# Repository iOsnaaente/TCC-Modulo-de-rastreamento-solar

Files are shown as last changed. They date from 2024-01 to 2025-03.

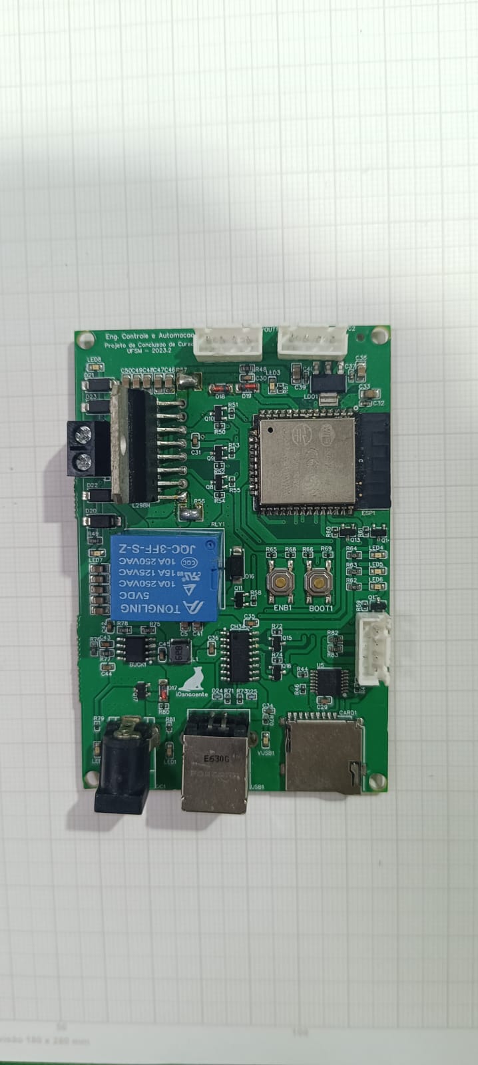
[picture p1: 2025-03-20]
Imagens/PCB_visão superior.jpg

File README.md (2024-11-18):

# TCC
Projeto de hardware para desenvolvimento de um módulo de controle de motor DC com sensor de posição angular para movimentação de paineis solares em dois eixos utilizando rede Modbus.

### Description 

The [bdc_motor](https://components.espressif.com/component/espressif/bdc_motor), 
The [PID component](https://components.espressif.com/component/espressif/pid_ctrl) is also managed by the component manager. 
These components' dependencies are listed in the [manifest file](main/idf_component.yml).

### Hardware Required

* A iOsnaaente TCC board with the ESP32-WROOM32E;
* A USB cable for Power supply and programming type micro-B;
* A separate 12 or 24V power supply for brushed DC motor;   
* H-bridge L298N datasheet used on board;
* A brushed DC motor connected in output borne on TCC board;
* A quadrature encoder of type AB to detect speed and direction of turns.

### Connection MCPWM + Encoder :
```
                              Battery power (8.4V - 24V)       
                                         |
      ESP 32                             v   L298N                   _
+-------------------+             +--------------------+            | |
|                   |             |      H-Bridge      |            | |
|               GND +<----------->| GND                |      +--------------+
|                   |             |      Chanel 1      |      |              |
|            GPIO_A +----GPIO0--->+ IN_A         OUT_A +----->|   Brushed    |
|            GPIO_B +----GPIO1--->+ IN_B               |      |     DC       |
|           BDC_PWM +----PWM0B--->+ PWM          OUT_B +----->|    Motor     |
|                   |             |                    |      |              |
|                   |             +--------------------+      |              |
|                   |                                         +------+-------+
|                   |                Encoder based                   |
|                   |                   on PCNT                      |
|                   |             +--------------------+             |
|            VCC3.3 +------------>+ VCC    Encoder     |             |
|                   |             |                    |             |
|               GND +<----------->+ GND                +<------------+
|                   |             |                    |
|         ENCODER_A |<---PCNT1----+ C1                 |
|         ENCODER_B |<---PCNT1----+ C2                 |
|                   |             |                    |
|                   |             |                    |
|                   |             |                    |
+-------------------+             +--------------------+
```

### MODBUS NETWORK 

Modbus multi slave segment connection schematic:

```
    MB_DEVICE_ADDR1
    -------------
    |           |
    |  Slave 1  |---<>--+
    |           |       |
    -------------       |
    MB_DEVICE_ADDR2     |
    -------------       |        -------------
    |           |       |        |           |
    |  Slave  2 |---<>--+---<>---|  Master   |
    |           |       |        |           |
    -------------       |        -------------
    MB_DEVICE_ADDR3     |
    -------------     Network (Ethernet or WiFi connection)
    |           |       |
    |  Slave 3  |---<>--+
    |           |
    -------------
```

### Steps 

[1] Fazer a definição dos pinouts de motores e encoders
    - IN1, IN2 e PWM para motores
    - ENC_A e ENC_B para o encoder de quadratura 

[2] Inicializar os pinouts apropriadamente 
    - Pinos de motores como OUTPUT
    - Pinos de sensor como INPUT 

[3] Inicializar as configurações do motor
    - Instaciar a struct motor_t 

[4] Inicializar as configurações do encoder
    - Instanciar a struct encoder_t 

[5] Criar a rotina de calculo da velocidade
    - Task ou Timer interrupt 

### Tutorials 

To learn more about Motor Controle PWM (MCPWM) see: 
[1] https://docs.espressif.com/projects/esp-idf/en/v4.4/esp32/api-reference/peripherals/mcpwm.html
[2] https://demo-dijiudu.readthedocs.io/en/latest/api-reference/peripherals/mcpwm.html

To learn more about Pulse CoNTer (PCNT) see: 
[1] https://demo-dijiudu.readthedocs.io/en/latest/api-reference/peripherals/mcpwm.html

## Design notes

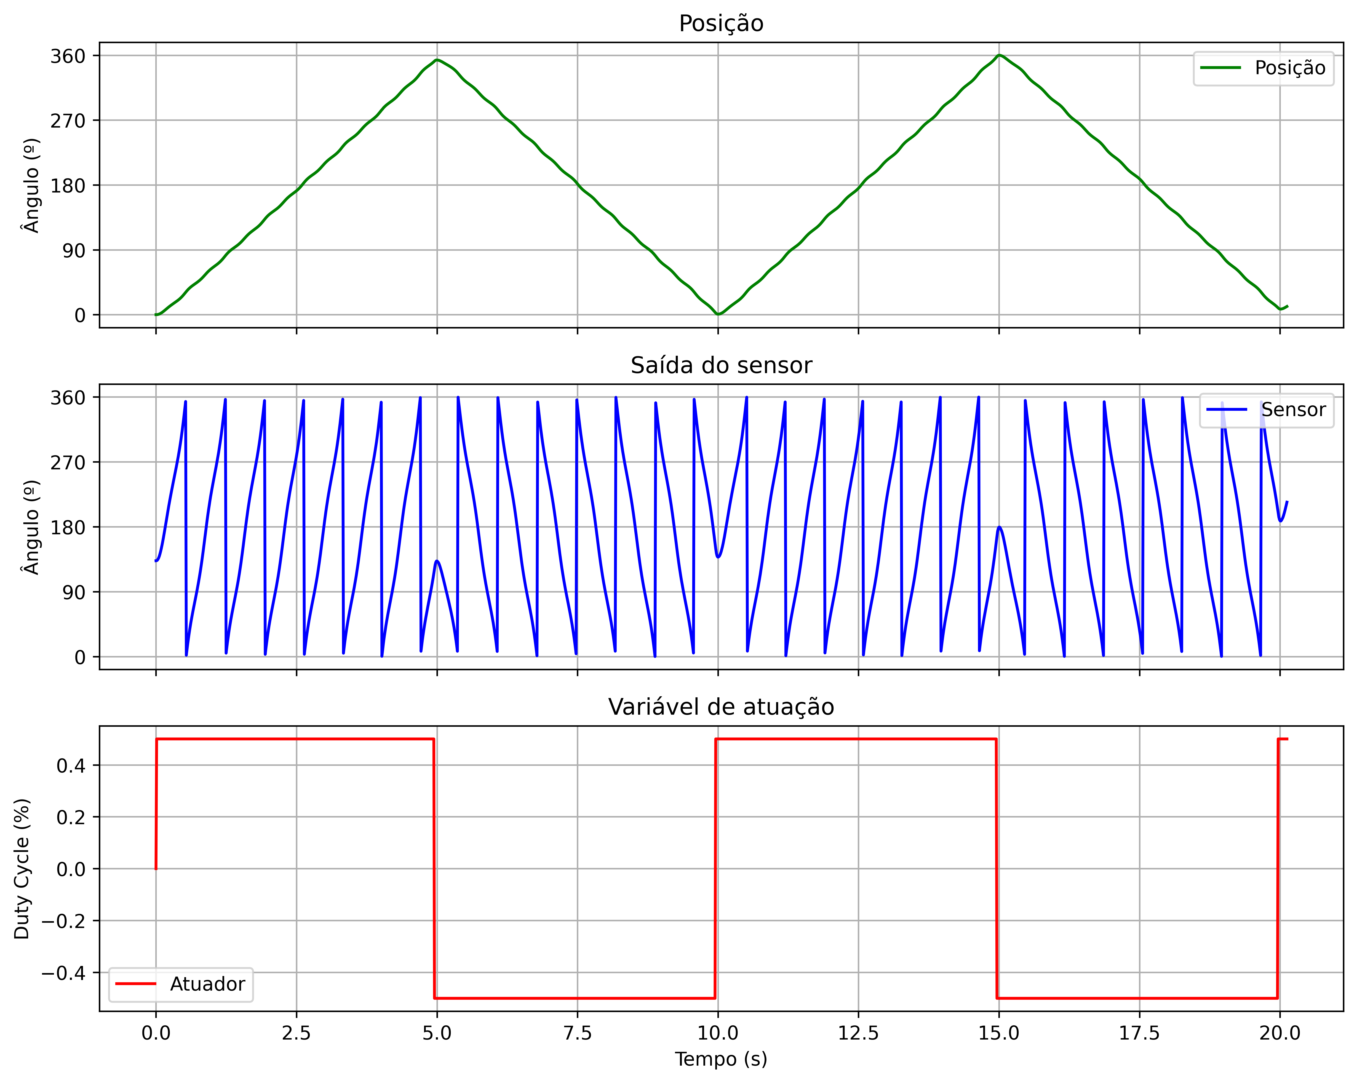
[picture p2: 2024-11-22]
Imagens/SensorMagnetico.png

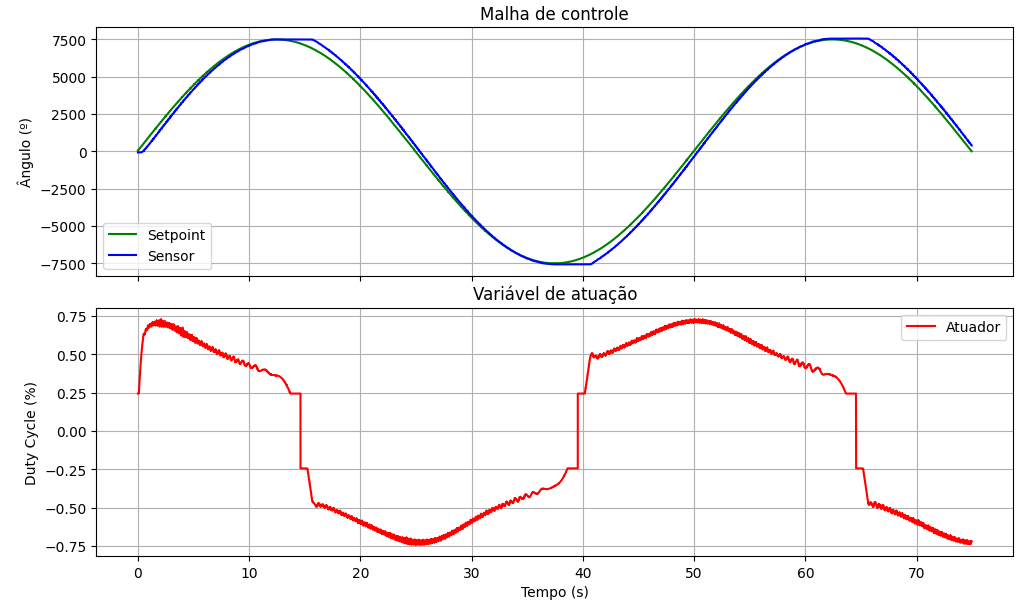
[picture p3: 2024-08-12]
Imagens/ControleSenoide.png

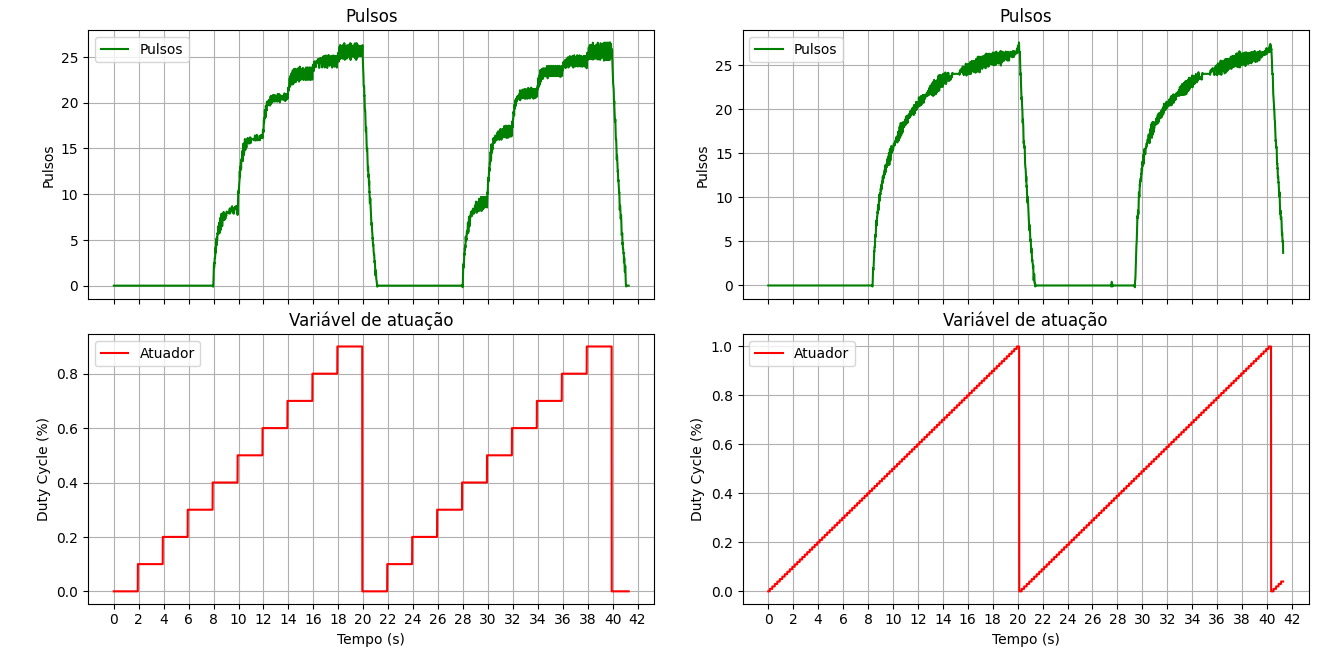
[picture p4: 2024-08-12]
Imagens/SensorIncremental.png

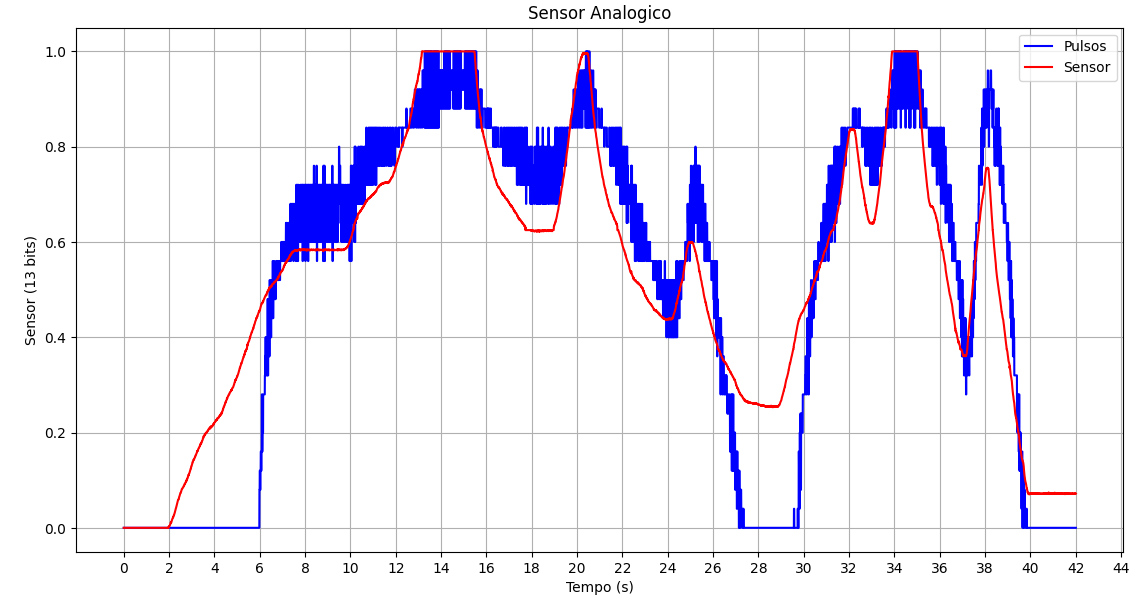
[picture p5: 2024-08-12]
Imagens/SensorAnalogico.png

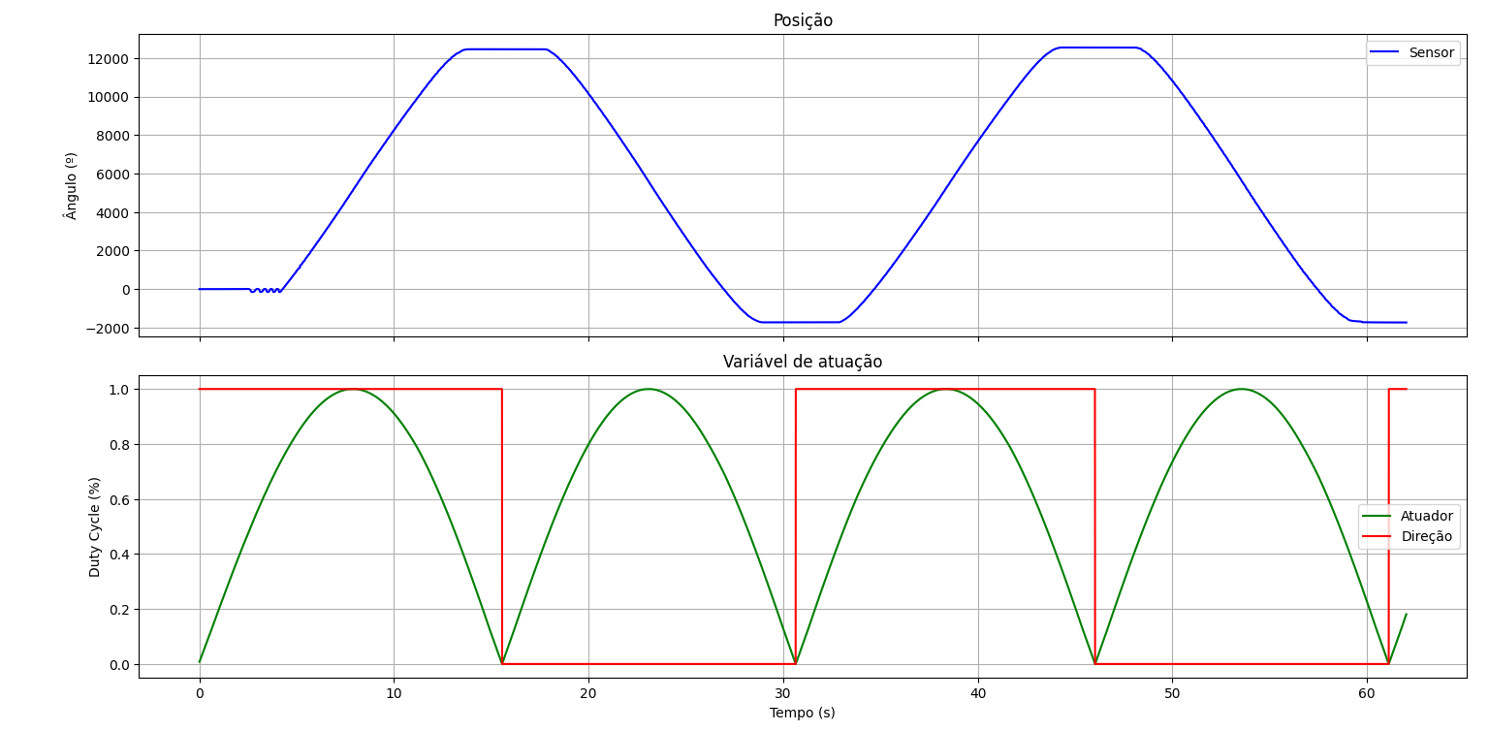
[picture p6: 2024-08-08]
Imagens/AtuadorDC.png

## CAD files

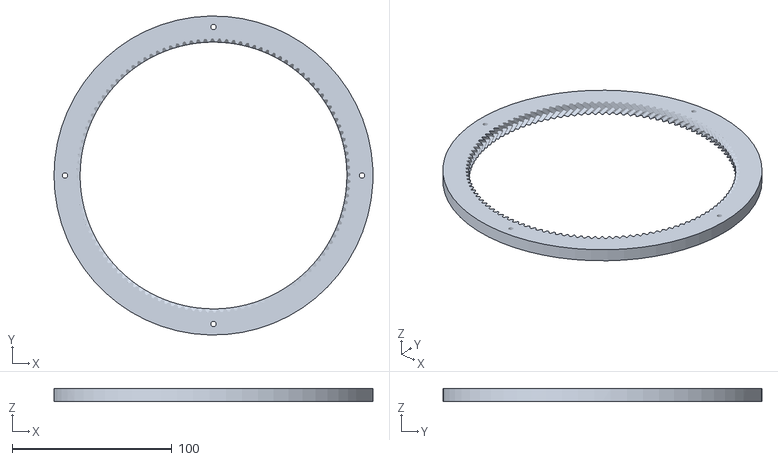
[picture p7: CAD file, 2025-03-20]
Modelos3D/3_Reducao_Anel.STL
200.0 x 199.9 x 8.00

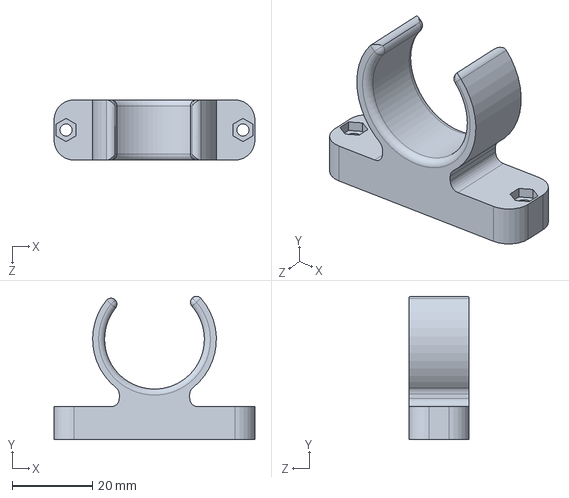
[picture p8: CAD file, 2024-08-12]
Modelos3D/3D/SUP_INC.SLDPRT
50.0 x 35.7 x 15.0 mm

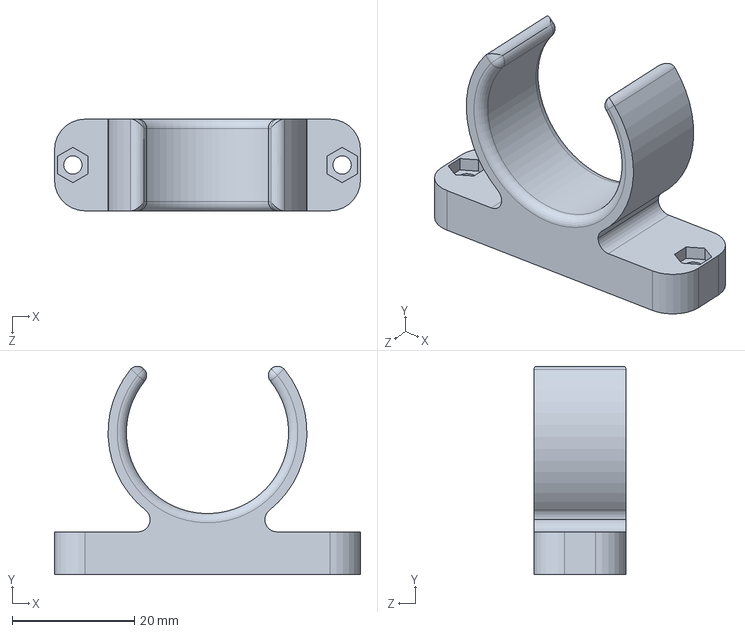
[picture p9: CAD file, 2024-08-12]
Modelos3D/3D/SUP_MAG.SLDPRT
50.0 x 34.1 x 15.0 mm

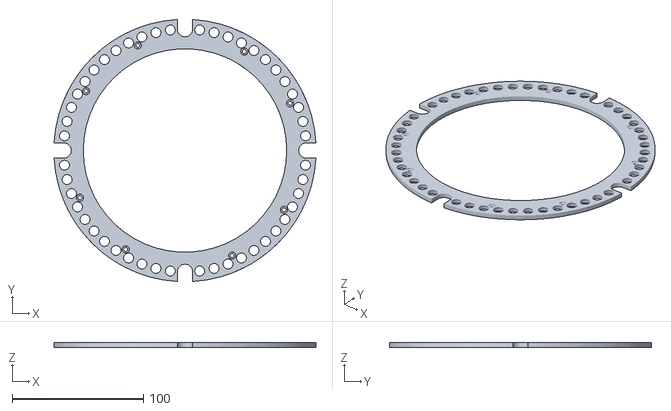
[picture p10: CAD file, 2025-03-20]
Modelos3D/Cópia de Peça2^Mont4.STL
199.7 x 199.7 x 3.50

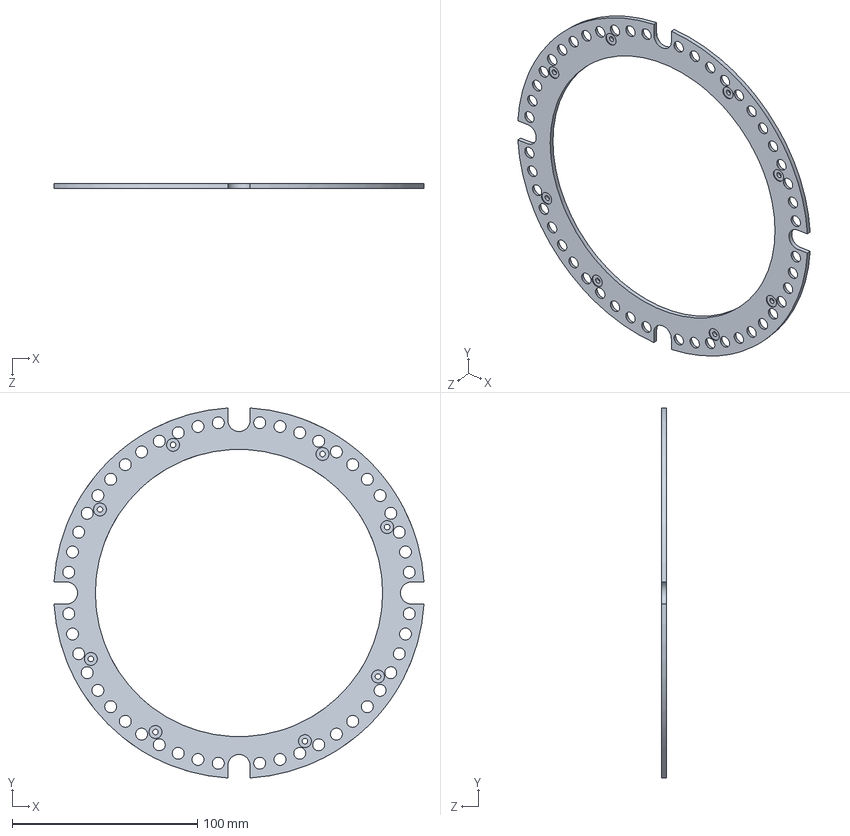
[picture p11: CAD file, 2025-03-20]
Modelos3D/Peça2^rolamentoCase2.SLDPRT
199.6 x 199.6 x 2.50 mm

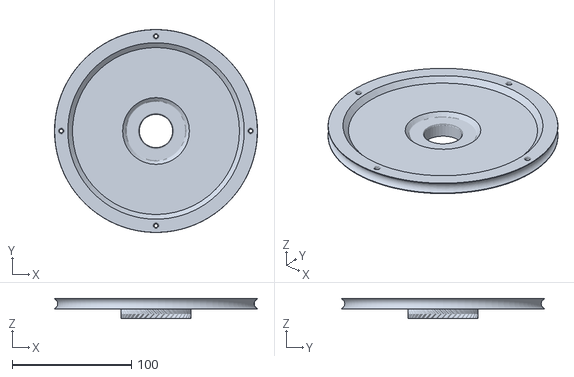
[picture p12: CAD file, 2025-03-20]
Modelos3D/anel_interno_Engrenagens.STL
170.2 x 170.1 x 17.0

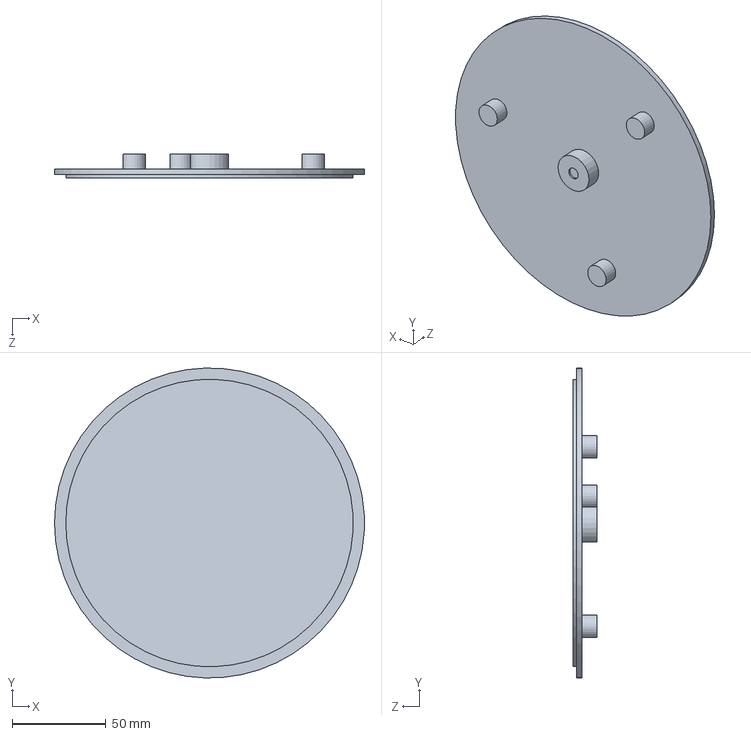
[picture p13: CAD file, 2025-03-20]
Modelos3D/P_Superior.SLDPRT
165.0 x 164.9 x 13.0 mm

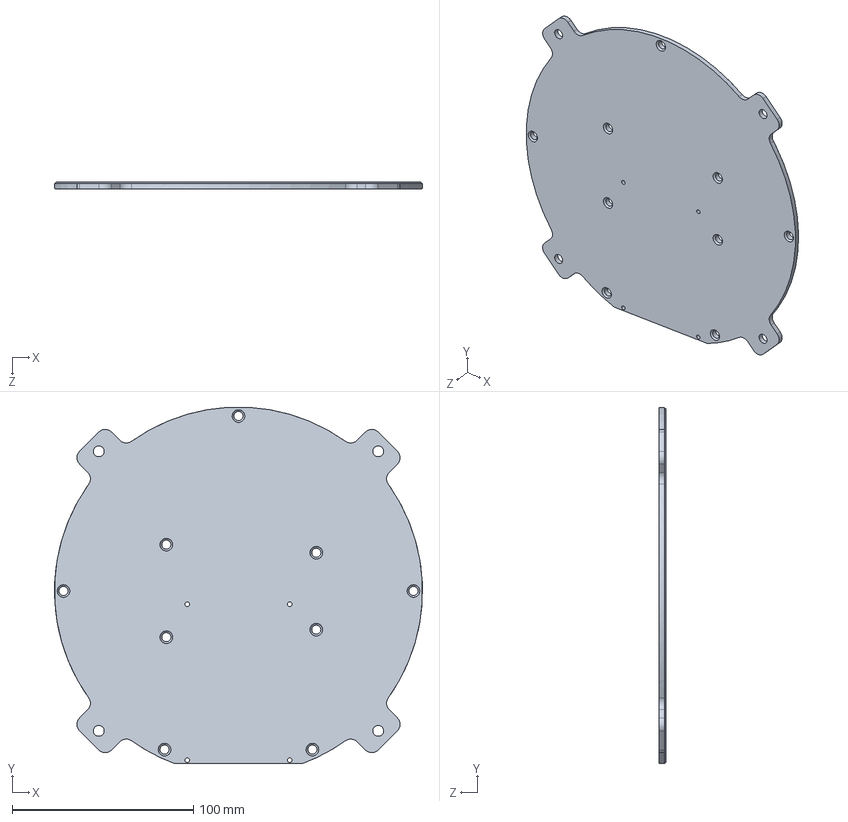
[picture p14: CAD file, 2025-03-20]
Modelos3D/Base_Estrutura.SLDPRT
203.0 x 196.6 x 4.00 mm

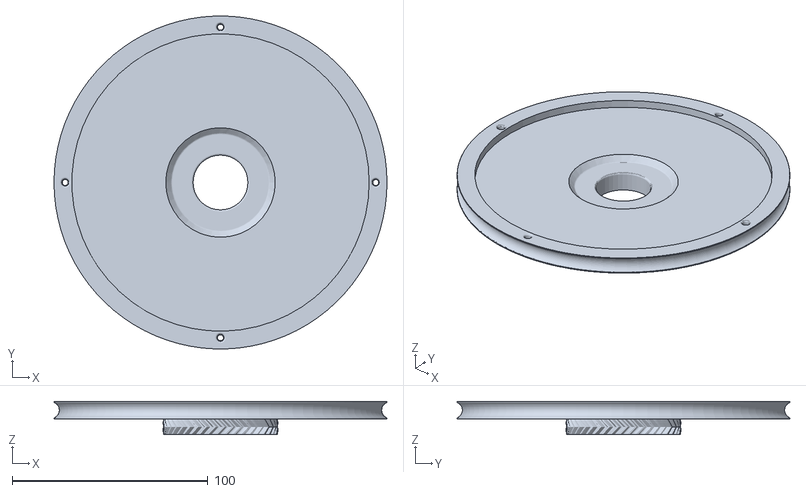
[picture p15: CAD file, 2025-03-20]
Modelos3D/1_Anel_Interno_Engrenagens.STL
170.2 x 170.1 x 17.0

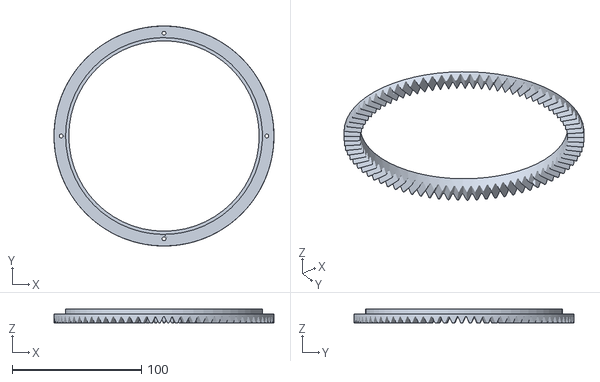
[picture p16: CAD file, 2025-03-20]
Modelos3D/2_Anel_Interno_Rosca.STL
169.9 x 169.9 x 11.0

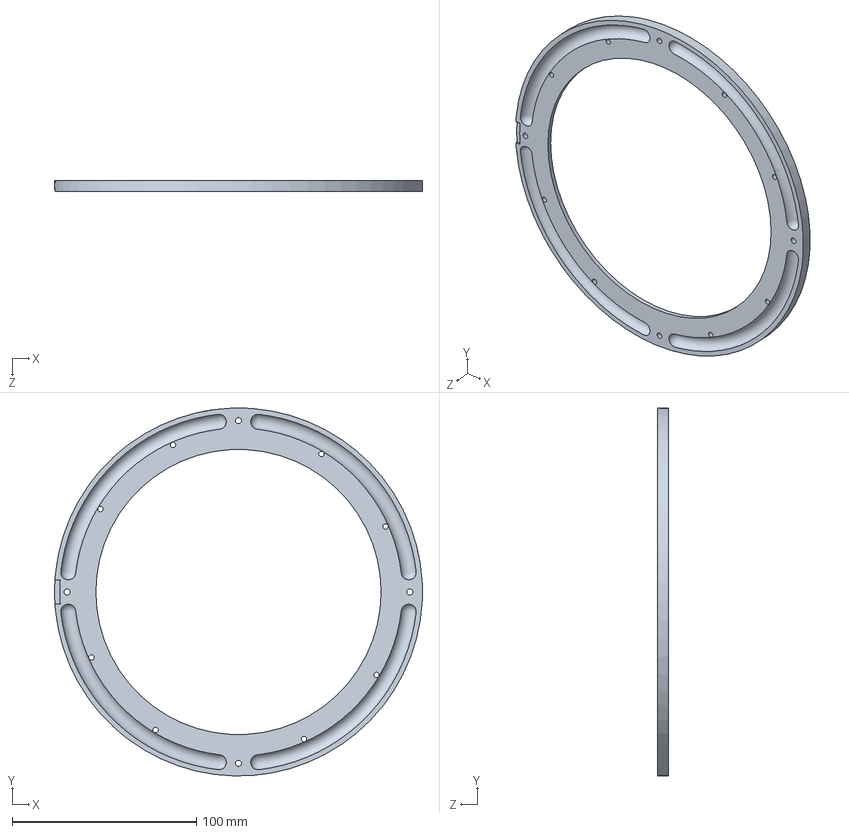
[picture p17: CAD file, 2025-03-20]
Modelos3D/P_Tampa1.SLDPRT
200.0 x 199.9 x 6.00 mm

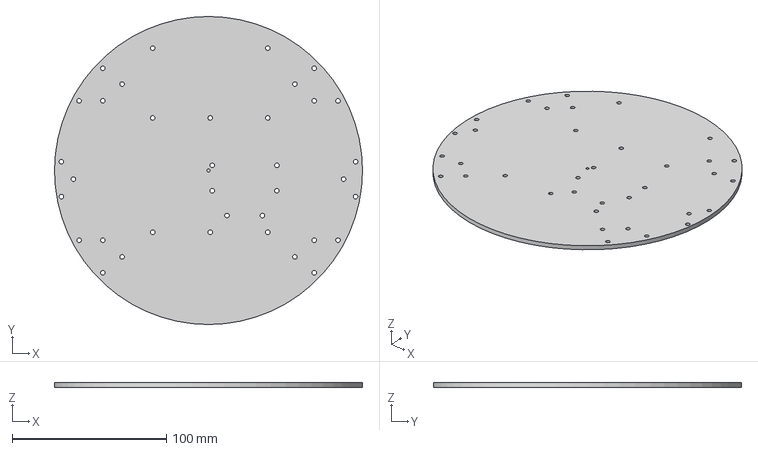
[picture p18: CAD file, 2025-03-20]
Modelos3D/furos.step
200.0 x 200.0 x 3.00 mm

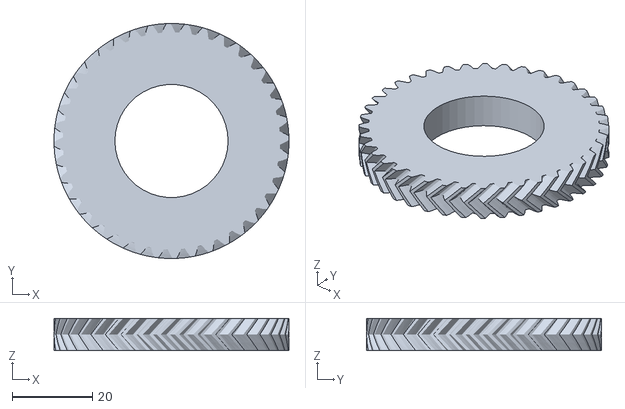
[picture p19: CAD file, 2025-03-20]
Modelos3D/Engrenagem_planeta.STL
58.6 x 58.6 x 8.00

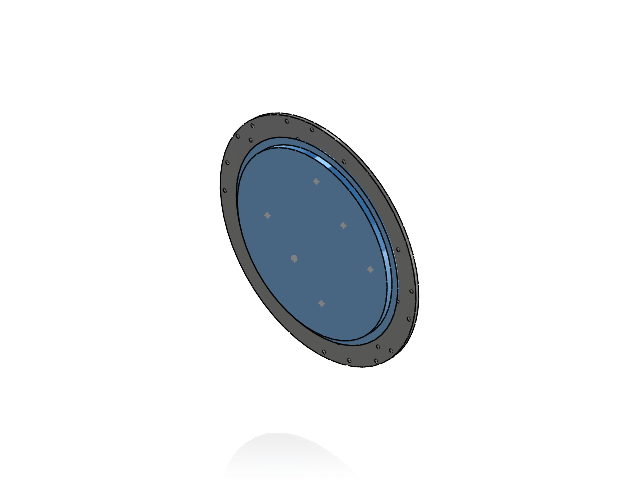
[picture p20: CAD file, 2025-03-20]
Modelos3D/Mont5.SLDASM
Superior
Componente27.step

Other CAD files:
Modelos3D/Reducao_Sol.SLDASM
Modelos3D/Mont4.SLDASM
Modelos3D/rolamentoCase.SLDASM
Modelos3D/Peça2^rolamentoCase.STL
Modelos3D/3D/SUP_INC.STL
Modelos3D/3D/SUP_MAG.STL
Modelos3D/Base_Estrutura.STL
Modelos3D/P_Tampa.SLDPRT
Modelos3D/P_Tampa.STL
Modelos3D/Superior.SLDPRT
Modelos3D/Superior.STL
Modelos3D/Tampa.SLDPRT
Modelos3D/Tampa.STL
Modelos3D/anel_interno_2.STL
Modelos3D/furos.SLDASM

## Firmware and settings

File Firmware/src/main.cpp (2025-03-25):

/**
  * @file main.cpp
  * @brief Entry Point do Firmware de controle 
  * @author Bruno Gabriel Flores Sampaio
  * @date 16 de março de 2025
  */

/** Board configurations */
#include "../board_config.h"

/** Controladores */
#include "controllers/includes/dataloggerController.h"
#include "controllers/includes/modbusController.h"
#include "controllers/includes/motorController.h"
#include "controllers/includes/serialController.h"

/** Módulos */
#include "modules/system/relay.h"


/** Objetos usados no sistema */
DataloggerController    *datalogger;
MotorController         *controller;
ModbusController        *modbus; 
Relay                   *relay;


// Contador para ser usado para debug
uint32_t debugger_counter = 0;

// Periodo para ser printado alguma informação via Terminal 
uint32_t debugger_period = 1000;

// Periodo do loop de verificação de estados 
uint32_t loop_period = 10;


void setup(){

    /** 
     * @brief Inicia a Serial para ser usada como Debug
     * @note Dentro de BoardConfig pode ser alterado o nível de Debug utilizado:
     * 1. DEBUG_SERIAL_COMPLETO 
     * 2. DEBUG_SERIAL_REDUZIDO 
     * 3. DEBUG_SERIAL_DESLIGADO 
    **/ 
    serial_begin( );

    /** 
     * @brief Inicia a comunicação WiFi para controle Modbus
     * 1. Inicia a interface Wi-Fi com Login e Senha definidos em BoardConfig
     * 2. Inicia a aplicação Modbus-TCP/IP utilizando a rede Wi-Fi
     * 3. Inicializa os registradores Modbus 
     * 4. Retorna o objeto Modbus para ser usado 
    **/ 
    DEBUG_SERIAL( "WIFI SSID", SSID_MASTER );
    modbus = new ModbusController( "ModbusController", RTC_SOFT );


    /** 
     * @brief Inicia o controle dos motores
     * @param description Descrição do objeto 
     * @param sensor_type Tipo de sensor para ser usado no módulo 
     * @param motor_type Tipo de motor utilizado no módulo 
     * 
     * 1. Inicializa a classe especifica do Sensor passado como parametro em SensorType_t 
     * 2. Inicializa a classe especifica do Motor passado como parametro em MotorType_t
     * 3. Cria a Task de controle de rastreamento do sistema
     * 
     * @note O tipo de rastreamento é dado pela MACRO definida em BoardConfig: 
     * - AZIMUTE_MODE - Modo de rastreio para Azimute 
     * - ZENITE_MODE - Modo de rastreio para Zenite 
    **/
    controller = new MotorController( "MotorController", SENSOR_AS5600_I2C, MOTOR_DC );  // controller->set_pid_gains( 10.25, 0.42, 4.78 );
    

    /**
     * @brief Define os valores de PID para a malha de controle do motor
     * @details A malha de controle é composta por um controlador em cascata, sendo composto por:
     * 1. Malha externa: Uma malha externa, que recebe o valor de referência do SP da planta (Posição);
     * 2. Malha interna: Uma malha interna que recebe a saída da primeira malha e faz o controle de velocidade do motor.
     * 
     * Dessa forma, a malha externa cuida da referência de posição, pois é a variavel de interesse do sistema e por consequencia,
     * é a malha mais lenta da planta, sua saída entra na malha de controle de velociade, uma malha rápida, que altera a
     * velocidade do motor para alcançar o objetivo do SP mais rápido.
     * 
     * Essa malha em cascata atingiu um bom resultado, sendo usado a medição de velocidade do motor ao invés do valor de 
     * corrente do mesmo, pois essa grandeza não pode ser medida de forma efetiva pelo módulo.   
     * 
     *                        double Kp, Ki, Kd
     **/ 
    controller->set_pos_pid_gains(  120.0, 100.0, 10.0 );
    // controller->set_vel_pid_gains(  1.0, 0.0, 0.0 );



    /** 
     * @brief Inicializa o Relé de proteção. 
    **/
    relay = new Relay( "Relay controller" );
    relay->turn_on();
    controller->stop();

    /** 
     * @brief Inicia a task do LED para debug visual
    **/
    xTaskCreate( &blink_Task, "BlinkTask", 1024*2, NULL, tskIDLE_PRIORITY, NULL );

}



/** 
 * @brief Loop principal 
 * 
 * Optou-se por utilizar o loop principal pois ele desempenha uma função simples, uma vez que as 
 * tarefas complexas de atuação, sensoriamento e controle do sistema, já estão sendo executadas
 * seguindo um Schedule do freeRTOS. 
 *  
 * A função do Loop esta relacionada com a comunicação Modbus do sistema, pois:
 * 1. Ele verifica de forma periodica se é necessário atualizar a Data e Hora do sistema;
 * 2. Ele verifica o estado de operação do sistema. 
 * 
 * @note Como o sistema será demonstrado como um caso de uso, criou-se estados de operação
 * que serão usados exclusivamente para a demonstração. Para uma aplicação real, pode-se criar 
 * estados mais complexos e que se adequem melhor à aplicação do mesmo.
 * 
 * Para a demonstração, será utilizado apenas um conjunto de estados que irão variar o SP da planta 
 * para valores fixos e conhecidos, permitindo mostrar a eficacia do sistema de controle e mostrando
 * que ele pode ser usado em um sistema de rastreamento solar. 
**/
void loop() {

    // Etapa 1: Verificar se é necessário atualizar a Data e Hora 
    if ( modbus->mb->Coil( COIL_DT_SYNC ) == true ){
        modbus->mb->Ireg( INPUT_YEAR,   modbus->mb->Hreg( HR_YEAR ) );
        modbus->mb->Ireg( INPUT_MONTH,  modbus->mb->Hreg( HR_MONTH ) );
        modbus->mb->Ireg( INPUT_DAY,    modbus->mb->Hreg( HR_DAY ) );  
        modbus->mb->Ireg( INPUT_HOUR,   modbus->mb->Hreg( HR_HOUR ) );
        modbus->mb->Ireg( INPUT_MINUTE, modbus->mb->Hreg( HR_MINUTE ) );
        modbus->mb->Ireg( INPUT_SECOND, modbus->mb->Hreg( HR_SECOND ) );
        modbus->mb->Coil( COIL_DT_SYNC, false );
    }

    // Etapa 2: Verifica os estados de operação do sistema 
    switch (modbus->mb->Hreg( HR_STATE ) ){


    /**
     * @brief Estado de operação Automático: COD: 0x00 
     * 
     * Neste estado de operação o sistema irá:
     * 1. Verificar se a Data e Hora do sistema estão atualizados 
     * 2. Iniciar a rotina de rastreio do SP através dos registradores Modbus 
    **/ 
    case HR_STATE_AUTO: 
        
        /**
         * Verifica se a Hora do sistema é válida
         * Se não for, então mantem o sistema desligado 
         */
        if ( modbus->mb->Ireg(INPUT_YEAR) <= 0 ) {
            controller->stop();
            relay->turn_off();

            if ( debugger_counter++ > (debugger_period / loop_period) ){
                debugger_counter = 0;
                DEBUG_SERIAL( "DATETIME", "Waiting datetime update" ); 
                vTaskDelay( pdMS_TO_TICKS(loop_period));
            }
        
        /**
         * Se a hora for válida, verifica se o Zenite é maior que Zero
         * Pois esse valor garante que o sistema deva estar em funcionamento
         * Se não for, o sistema deverá ir para o estado de GO_HOME 
         */
        }else{
            if ( ((int16_t) modbus->mb->Ireg(INPUT_ZENITH)) >= 0.0  ) { 
                controller->start();
                relay->turn_on();
                controller->set_target( modbus->mb->Ireg(INPUT_SUN_TARGET) );
            }else {
                modbus->mb->Hreg( HR_STATE, HR_STATE_GO_HOME ); 
            }        
        }
        break;


    /**
     * @brief Estados de operação por Quadrante: 
     * 
     * Nestes estados de operação o sistema irá possuir um SP fixo
     * determinados pelos valores de HR_QUADRANT_X_ANGLE.
     * 
     * Os valores dos quadrantes estão definidos em ModbusController.h 
     * 
     * HR_QUADRANT_1_ANGLE   ((float)(0.000))
     * HR_QUADRANT_2_ANGLE   ((float)(90.00))
     * HR_QUADRANT_3_ANGLE   ((float)(180.0))
     * HR_QUADRANT_4_ANGLE   ((float)(270.0))
     * HR_QUADRANT_12_ANGLE  ((float)(45.00))
     * HR_QUADRANT_23_ANGLE  ((float)(135.0))
     * HR_QUADRANT_34_ANGLE  ((float)(225.0))
     * HR_QUADRANT_41_ANGLE  ((float)(315.0))
    **/ 
    case HR_STATE_QUADRANT_1: // COD: 0x01
        controller->start();
        controller->set_target( HR_QUADRANT_1_ANGLE );
        modbus->mb->Ireg(INPUT_SUN_TARGET, HR_QUADRANT_1_ANGLE );
        break;
    case HR_STATE_QUADRANT_2: // COD: 0x02
        controller->start();
        controller->set_target( HR_QUADRANT_2_ANGLE );
        modbus->mb->Ireg(INPUT_SUN_TARGET, HR_QUADRANT_2_ANGLE );
        break;
    case HR_STATE_QUADRANT_3: // COD: 0x03
        controller->start();
        controller->set_target( HR_QUADRANT_3_ANGLE );
        modbus->mb->Ireg(INPUT_SUN_TARGET, HR_QUADRANT_3_ANGLE );
        break;
    case HR_STATE_QUADRANT_4: // COD: 0x04
        controller->start();
        controller->set_target( HR_QUADRANT_4_ANGLE );
        modbus->mb->Ireg(INPUT_SUN_TARGET, HR_QUADRANT_4_ANGLE );
        break;

    case HR_STATE_QUADRANT_12: // COD: 0x12
        controller->start();
        controller->set_target( HR_QUADRANT_12_ANGLE );
        modbus->mb->Ireg(INPUT_SUN_TARGET, HR_QUADRANT_12_ANGLE );
        break;
    case HR_STATE_QUADRANT_23: // COD: 0x23
        controller->start();
        controller->set_target( HR_QUADRANT_23_ANGLE );
        modbus->mb->Ireg(INPUT_SUN_TARGET, HR_QUADRANT_23_ANGLE );
        break;
    case HR_STATE_QUADRANT_34: // COD: 0x34
        controller->start();
        controller->set_target( HR_QUADRANT_34_ANGLE );
        modbus->mb->Ireg(INPUT_SUN_TARGET, HR_QUADRANT_34_ANGLE );
        break;
    case HR_STATE_QUADRANT_41: // COD: 0x41
        controller->start();
        controller->set_target( HR_QUADRANT_41_ANGLE );
        modbus->mb->Ireg(INPUT_SUN_TARGET, HR_QUADRANT_41_ANGLE );
        break;
    
    case 127:
        controller->motor->set_direction( BDC_FORWARD );
        controller->motor->set_speed(BDC_MAX_POWER);
    
    case 126:
    case 128:
        controller->motor->set_direction( BDC_BACKWARD );
        controller->motor->set_speed(BDC_MAX_POWER);

    /** 
     * @brief Estado de operação de retorno para casa: COD: 0xFD
     * Retorna o sistema para uma posição inicial conhecida para iniciar a rotina de rastreio
     */
    case HR_STATE_GO_HOME:
        controller->start();
        relay->turn_on();
        controller->set_target( POS_HOME_MIN );
        if ( 
            modbus->mb->Ireg(INPUT_SENSOR_POS) > POS_HOME_MIN && 
            modbus->mb->Ireg(INPUT_SENSOR_POS) < POS_HOME_MAX   
        ){
            modbus->mb->Hreg( HR_STATE, HR_STATE_WAITING );
            DEBUG_SERIAL( "HOME", "POSITION REACHED" );
        }

    /** 
     * @brief Estado de operação aguarda na posição HOME: COD: 0xFE
     */
    case HR_STATE_WAITING:
        controller->stop();
        relay->turn_off();
        if ( ((int16_t) modbus->mb->Ireg(INPUT_ZENITH)) >= 0.0  ) {
            modbus->mb->Hreg( HR_STATE, HR_STATE_AUTO ); 
            DEBUG_SERIAL( "INICITIATE", "Starting Tracking. Good Morning SM!" );             
        } 


    /**
     * @brief Estado de operação DESLIGADO. COD: 0xFF
    **/
    case HR_STATE_OFF:
    default:
        controller->stop();
        break;
    }


    // Debug 
    if ( debugger_counter++ > (debugger_period / loop_period) ){
        debugger_counter = 0;
        DEBUG_SERIAL( "SYSTEM STATE"  , modbus->mb->Hreg( HR_STATE ) ); 
        DEBUG_SERIAL( "GOAL POSITION"  , modbus->mb->Ireg(INPUT_SUN_TARGET) ); 
        DEBUG_SERIAL( "MOTOR POSITION" , controller->position ); 
        DEBUG_SERIAL( "MOTOR SPEED %"  , controller->motor->speed ); 
        Serial.println(WiFi.localIP());
    }
    modbus->mb->Ireg( INPUT_SENSOR_POS, (float)controller->sensor->scaled_position );
    vTaskDelay( pdMS_TO_TICKS( loop_period ) );
}


/** Task de Led blink */
void blink_Task(void *pvParameters) {
    gpio_set_direction( LED_BOARD, (gpio_mode_t) GPIO_MODE_OUTPUT );
    bool state = false;
    while(true) {
        gpio_set_level(LED_BOARD, state = !state );
        vTaskDelay( pdMS_TO_TICKS(500));
    }
}

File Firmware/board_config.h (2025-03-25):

/**
 * @file board_config.h
 * @brief Gerenciador das configurações do código utilizado no projeto
 * de conclusão de curso TCC em Engenharia de controle e automação. 
 * @author Bruno Gabriel Flores Sampaio,
 * @date 22 de julho de 2024
 */


#ifndef BOARDs_CONFIG_H_
#define BOARDs_CONFIG_H_

#include "freertos/FreeRTOS.h"
#include "freertos/queue.h"
#include "freertos/semphr.h"
#include "freertos/task.h"

#include "driver/gpio.h"


/** Posição geográfica */
#define LATITUDE    -29.16530765942215
#define LONGITUDE   -54.89831672609559

/* Velocidade de comunicação entre Debug */
#define UART_BAUDRATE 115200     


/** UNCOMMENT ONE OF THAT TO USE IN SYSTEM */
// #define AZIMUTE_MODE
#define ZENITE_MODE



/**
 * @brief Configurações do Wi-Fi
 * @details É necessário se definir as credenciais da rede WiFi
 * TODO: Implementar um WiFiManager para configurar a rede WiFi 
 *       sem a necessidade de recompilar o código.
 *       Ou então, implementar um armazenamento na memória não volátil
 */
#define SSID_MASTER         ((const char *)"Tracker-TCC")
#define PSD_MASTER          ((const char *)"Bruno123456")

#define SERVER_IP           ((const char *)"10.0.0.120")
#define SERVER_PORT         502


#define I2C_RX_BUFFER       1024
#define I2C_TX_BUFFER       1024 
#define I2C_BUS_TIMEOUT_MS  50 


/** 
 * @brief Mensagem de debug para serial. 
 * @details É usado um Mutex para não haver conflitos de uso de memórias compartilhadas e deadlocks
 * Para desativar o debug serial, deve ser definido a Macrodefinição DEBUG_SERIAL_DESLIGADO
 * 
 * @example `#define DEBUG_SERIAL_COMPLETO`  -> Printa o nome do arquivo e linha + mensagem de debug
 * @example `#define DEBUG_SERIAL_REDUZIDO`  -> Printa somente a mensagem de debug
 * @example `#define DEBUG_SERIAL_DESLIGADO` -> Desliga o print de mensagens de debug 
 */

// #define DEBUG_SERIAL_COMPLETO 
#define DEBUG_SERIAL_REDUZIDO 
// #define DEBUG_SERIAL_DESLIGADO 


/**
 * @brief GPIO do LED da placa 
 */ 
#define LED_BOARD         ((gpio_num_t)GPIO_NUM_2)

/* ADC com soquete externo - Sensores */
#define ADC_EXT1          ((gpio_num_t)GPIO_NUM_36)
#define ADC_EXT2          ((gpio_num_t)GPIO_NUM_39)
#define ADC_EXT3          ((gpio_num_t)GPIO_NUM_34)

#define ADC_EXT1_CHANNEL  ((adc1_channel_t)ADC1_CHANNEL_0)
#define ADC_EXT2_CHANNEL  ((adc1_channel_t)ADC1_CHANNEL_3)
#define ADC_EXT3_CHANNEL  ((adc1_channel_t)ADC1_CHANNEL_6)

/* ADCs internos  */
#define ADC4              ((gpio_num_t)GPIO_NUM_35)
#define ADC5              ((gpio_num_t)GPIO_NUM_33)
#define ADC6              ((gpio_num_t)GPIO_NUM_25)

#define ADC4_CHANNEL      ((adc1_channel_t)ADC1_CHANNEL_7)
#define ADC5_CHANNEL      ((adc1_channel_t)ADC1_CHANNEL_5)
#define ADC6_CHANNEL      ((adc2_channel_t)ADC2_CHANNEL_8)

/* GPIO de controle do Relé de potência  */
#define POWER_RELAY       ((gpio_num_t)GPIO_NUM_32)

/* Interface SPI - Leitor de cartão micro SD  */
#define BOARD_MOSI        ((gpio_num_t)GPIO_NUM_23) 
#define BOARD_MISO        ((gpio_num_t)GPIO_NUM_19)
#define BOARD_CS          ((gpio_num_t)GPIO_NUM_15)
#define BOARD_SCK         ((gpio_num_t)GPIO_NUM_18)

/* Interface I2C com soquete externo */
#define BOARD_SDA         ((gpio_num_t)GPIO_NUM_21)
#define BOARD_SCL         ((gpio_num_t)GPIO_NUM_22)


/* GPIO para ponte H - L298N */
#define IN1               ((gpio_num_t)GPIO_NUM_17)
#define IN2               ((gpio_num_t)GPIO_NUM_16)
#define ENB               ((gpio_num_t)GPIO_NUM_4)

/* ADC de leitura de corrente da ponte H  */
#define I_SENSING         ((gpio_num_t)GPIO_NUM_33)

/* GPIO com soquete externo - Sensores  */
#define GPIO_EXT1         ((gpio_num_t)GPIO_NUM_26)
#define GPIO_EXT2         ((gpio_num_t)GPIO_NUM_27)
#define GPIO_EXT3         ((gpio_num_t)GPIO_NUM_14)

#define UART_TXD0         ((gpio_num_t)GPIO_NUM_1)
#define UART_RXD0         ((gpio_num_t)GPIO_NUM_3)


/** Protótipo de funções auxiliares */
void blink_Task(void *pvParameters);

#endif

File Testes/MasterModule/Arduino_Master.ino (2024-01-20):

#include "freertos/event_groups.h"
#include "freertos/FreeRTOS.h"
#include "freertos/task.h"
#include "esp_system.h"
#include "esp_wifi.h"
#include <esp_log.h>
#include <stdio.h>

#include "registradores.h"

#include <ModbusIP_ESP8266.h>
#include <DS3231.h>
#include <Wire.h>

#include <WiFi.h>


#define UNKNOW 0   // Operation mode
#define AZIMUTH 1  // Operation mode
#define ZENITH 2   // Operation mode

DS3231 rtc;
ModbusIP mb;

// Defina as credenciais do ponto de acesso
IPAddress AP_IP(192, 168, 12, 1);
const char *SSID_MASTER = "ESP32_TCC_MASTER_MODBUS";
const char *PSD_MASTER = "12051999";


wifi_sta_list_t wifi_sta_list;
tcpip_adapter_sta_list_t adapter_sta_list;

// Defina o número máximo de clientes conforme necessário
const int MAX_CLIENTS = 32;

// Gerenciamento de novos clientes
struct client_params_t {
  uint8_t sta_aid;
  uint8_t sta_mac[6];
  esp_ip4_addr_t sta_ip;
  bool sta_connected;
  uint8_t sta_mode;
  bool sta_datetime_sync;
};
client_params_t clients[MAX_CLIENTS];

bool flag_clients_to_sync = false;

// Modbus array data
uint16_t modbus_data[6];

uint32_t count = 0;
bool century = false;
bool h12Flag;
bool pmFlag;


// Handler das conexões entre dispositivos
static void wifi_event_handler(void *args, esp_event_base_t event_base, int32_t event_id, void *event_data) {
  // Quando uma nova STA é conectada ela é adicionada à lista de clientes
  if (event_base == WIFI_EVENT && event_id == WIFI_EVENT_AP_STACONNECTED) {
    wifi_event_ap_staconnected_t *sta_connected = (wifi_event_ap_staconnected_t *)event_data;
    for (uint8_t i = 0; i < MAX_CLIENTS; i++) {
      if (!clients[i].sta_connected) {
        clients[i].sta_aid = sta_connected->aid;
        memcpy(clients[i].sta_mac, sta_connected->mac, sizeof(clients[i].sta_mac));
        clients[i].sta_ip = { 0 };
        clients[i].sta_connected = true;
        clients[i].sta_mode = UNKNOW;
        clients[i].sta_datetime_sync = true;
        printf("New client connected!\nAID: %d\n", clients[i].sta_aid);
        break;
      }
    }

    // Quando uma STA é desconectada ela é removida da lista de clientes
  } else if (event_base == WIFI_EVENT && event_id == WIFI_EVENT_AP_STADISCONNECTED) {
    wifi_event_ap_stadisconnected_t *sta_disconnected = (wifi_event_ap_stadisconnected_t *)event_data;
    for (uint8_t i = 0; i < MAX_CLIENTS; i++)
      if (!clients[i].sta_aid == sta_disconnected->aid)
        clients[i] = { 0 };
    printf("Client with AID:%d disconnected!\n", sta_disconnected->aid);

    // Quando um cliente recebe um IP, ele é associado dentro da lista de clientes relacionado a ele
  } else if (event_base == IP_EVENT && event_id == IP_EVENT_AP_STAIPASSIGNED) {
    printf("AP STA IP ASSIGNED...\n");
    // Prepara uma lista para salvar os STA conectados
    memset(&wifi_sta_list, 0, sizeof(wifi_sta_list));
    memset(&adapter_sta_list, 0, sizeof(adapter_sta_list));
    esp_wifi_ap_get_sta_list(&wifi_sta_list);
    tcpip_adapter_get_sta_list(&wifi_sta_list, &adapter_sta_list);
    // Compara com os STAs já conectados
    for (uint8_t i = 0; i < adapter_sta_list.num; i++) {
      tcpip_adapter_sta_info_t sta = adapter_sta_list.sta[i];
      for (uint8_t j = 0; j < MAX_CLIENTS; j++) {
        if (clients[j].sta_aid && !memcmp(clients[j].sta_mac, sta.mac, sizeof(clients[j].sta_mac))) {
          clients[i].sta_ip = sta.ip;
          printf("Cliente AID:%d encontrado pelo MAC.\nIP associado: %s \n", clients[i].sta_aid, ip4addr_ntoa((const ip4_addr_t *)&(sta.ip)));
          break;
        }
      }
    }
    flag_clients_to_sync = true;
  }
}

void setup() {
  // Inicializa o Serial
  Serial.begin(115200);
  printf("esp idf version:%s \n\r", esp_get_idf_version());
  memset(&wifi_sta_list, 0, sizeof(wifi_sta_list));
  memset(&adapter_sta_list, 0, sizeof(adapter_sta_list));


  // Inicializa o barramento I2C
  Wire.begin();
  printf("Wire began!\n");
  // Atualiza a hora se necessário
  // set_datetime();


  // Inicializa o AP
  WiFi.softAPConfig(AP_IP, AP_IP, IPAddress(255, 255, 255, 0));
  WiFi.softAP(SSID_MASTER, PSD_MASTER);


  // Registrar os callbacks para eventos WiFi
  esp_event_handler_instance_register(WIFI_EVENT, ESP_EVENT_ANY_ID, &wifi_event_handler, NULL, NULL);
  esp_event_handler_instance_register(IP_EVENT, ESP_EVENT_ANY_ID, &wifi_event_handler, NULL, NULL);
  printf("Server AP inicilizated!\nIP do Access Point: %s\n", WiFi.softAPIP());

  // Inicia o Modbus
  mb.client();
  printf("Modbus cliente (Master) inicilizated!\n");
}

void loop() {

  // Execute as tarefas do Modbus
  mb.task();

  // Verifica se os clientes estão sincronizados ou não
  for (int i = 0; i < MAX_CLIENTS; i++) {
    if (clients[i].sta_datetime_sync) {
      // printf("Client[AID:%d] have to sync!\n", clients[i].sta_aid);
      IPAddress clientIP(clients[i].sta_ip.addr);  // clients[i].sta_ip é do tipo esp_ip4_addr e precisa ser IPAddress
      if (!mb.isConnected(clientIP)) {
        mb.connect(clientIP);
      }
      mb.writeHreg(clientIP, HR_YEAR, modbus_data, 6);
      mb.writeCoil(clientIP, COIL_DT_SYNC, true);
      bool ret_mb[1] = { 0 };
      mb.readCoil(clientIP, COIL_DT_SYNC, ret_mb, 1);
      if (ret_mb[0]) {
        Serial.println("Flag_clients_to_sync atualizada com base no COIL_DT_SYNC!");
        clients[i].sta_datetime_sync = false;
      }
    }
  }
  // Atualiza a aproximadamente 1s
  if ((count++) % 10 == 0)
    update_datetime();
  vTaskDelay(pdMS_TO_TICKS(100));
}


void set_datetime(void) {
  rtc.setClockMode(false);  // set to 24h
  rtc.setYear(24);
  rtc.setMonth(1);
  rtc.setDate(10);
  rtc.setDoW(3);
  rtc.setHour(18);
  rtc.setMinute(12);
  rtc.setSecond(0);
  printf("datetime updated!\n");
}

void update_datetime(void) {
  // Atualiza a array de data
  modbus_data[0] = rtc.getYear();
  modbus_data[1] = rtc.getMonth(century);
  modbus_data[2] = rtc.getDate();
  modbus_data[3] = rtc.getHour(h12Flag, pmFlag);
  modbus_data[4] = rtc.getMinute();
  modbus_data[5] = rtc.getSecond();
  // Impressão formatada usando printf
  printf("%d-%d-%d %d:%d:%d\n", modbus_data[0], modbus_data[1], modbus_data[2], modbus_data[3], modbus_data[4], modbus_data[5]);
}

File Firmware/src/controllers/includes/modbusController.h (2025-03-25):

/**
  * @file modbus.h
  * @brief Classe de uso modbus. 
  * @author Bruno Gabriel Flores Sampaio, 
  * @date 23 de julho de 2024
  */

#ifndef _MODBUS_H_ 
#define _MODBUS_H_ 

/* Importar a biblioteca externa */
#include "ModbusIP_ESP8266.h"


#include "freertos/FreeRTOS.h"
#include "freertos/semphr.h"
#include "freertos/task.h"

#include <esp_wifi.h>
#include <esp_system.h>
#include <esp_event.h>
#include <esp_netif.h>

#include "esp_chip_info.h"
#include "esp_mac.h"

#include <nvs_flash.h>

/* Configurações de placa */
#include "../../../board_config.h"

/* Módulos */ 
#include "../../modules/spa/spa.h"
#include "../../modules/rtcs/softRTC.h"
#include "../../modules/rtcs/ds3231.h"

/* Interfaces */ 
#include "../../interfaces/RTC.h"


#include "serialController.h"

/*
 * +-----------------------+-----------------+---------------------------------------------+
 * | Coil/Register Numbers |  Data Addresses |       Type	Table Name                       |
 * +-----------------------+-----------------+---------------------------------------------+
 * |        1-9999         |  0000 to 270E   | Read-Write	Discrete Output Coils            |   
 * |      10001-19999      |  0000 to 270E   | Read-Only	Discrete Input Contacts          |     
 * |      30001-39999      |  0000 to 270E	 | Read-Only	Analog Input Registers           |     
 * |      40001-49999      |  0000 to 270E	 | Read-Write	Analog Output Holding Registers  |             
 * +------------------------+----------------+---------------------------------------------+
 */
#define COIL_REG_OFFSET           1      // Modbus COIL     reg Offset
#define DISCRETE_REG_OFFSET   10000      // Modbus DISCRETE reg Offset
#define ANALOG_REG_OFFSET     20000      // Modbus ANALOG   reg Offset
#define HOLDING_REG_OFFSET    30000      // Modbus HOLDING  reg Offset


// MODBUS INPUTS REGISTER ADDRESSES
#define INPUT_SYSTEM_MODE    0x00

#define INPUT_SENSOR_STATUS  0x01
#define INPUT_SENSOR_POS     0x02

#define INPUT_SUN_TARGET     0x04
#define INPUT_ZENITH         0x06
#define INPUT_AZIMUTH        0x08

#define INPUT_POWER_GEN  	   0x0A   
#define INPUT_TEMPERATURE    0x0C
#define INPUT_PRESURE        0x0E

#define INPUT_YEAR           0x10
#define INPUT_MONTH          0x11
#define INPUT_DAY            0x12
#define INPUT_HOUR           0x13
#define INPUT_MINUTE         0x14
#define INPUT_SECOND         0x15



// MODBUS HOLDING REGISTER ADDRESSES
#define HR_STATE             0x00

#define HR_MOTOR_PV          0x01
#define HR_MOTOR_KP          0x03
#define HR_MOTOR_KI          0x05
#define HR_MOTOR_KD          0x07

#define HR_ALTITUDE          0x09
#define HR_LATITUDE          0x0B
#define HR_LONGITUDE         0x0D

#define HR_YEAR              0x0F
#define HR_MONTH             0x10
#define HR_DAY               0x11
#define HR_HOUR              0x12
#define HR_MINUTE            0x13
#define HR_SECOND            0x14


// MODBUS DISCRETES REGISTER ADDRESSES
#define DISCRETE_ADC1_0      0x00
#define DISCRETE_ADC1_3      0x01
#define DISCRETE_ADC1_6      0x03

#define DISCRETE_FAIL        0x04
#define DISCRETE_SYNC        0x05


// MODBUS COILS REGISTER ADDRESSES
#define COIL_POWER           0x00   
#define COIL_LED             0x01
#define COIL_DT_SYNC         0x02
#define COIL_PUSH_BUTTON_1   0x03
#define COIL_PUSH_BUTTON_2   0x04
#define COIL_PUSH_BUTTON_3   0x05



/* *
 * +----------------+-------------+-------------------------------------------------+
 * | Function Code	|    Action	  |          Table Name                             |
 * +----------------+-------------+-------------------------------------------------+
 * |      01        |   (01 hex)	|  Read	Discrete Output Coils                     |
 * |      02        |   (02 hex)	|  Read	Discrete Input Contacts                   |
 * |      03        |   (03 hex)	|  Read	Analog Output Holding Registers           |
 * |      04        |   (04 hex)	|  Read	Analog Input Registers                    |
 * |      05        |   (05 hex)	|  Write single	Discrete Output Coil              |
 * |      06        |   (06 hex)	|  Write single	Analog Output Holding Register    |
 * |      15        |   (0F hex)	|  Write multiple	Discrete Output Coils           |
 * |      16        |   (10 hex)	|  Write multiple	Analog Output Holding Registers |
 * +----------------+-------------+-------------------------------------------------+
 * */
#define READ_COIL                 0x01
#define READ_DISCRETE             0x02
#define READ_HOLDING              0x03
#define READ_ANALOG               0x04
#define WRITE_SINGLE_COIL         0x05
#define WRITE_SINGLE_HOLDING      0x06
#define WRITE_MULTIPLE_COILS      0x0F
#define WRITE_MULTIPLE_HOLDINGS   0x10

/* *
 * AE41 5652  ->  high byte first / high word first  = "big endian"
 * 5652 AE41  ->  high byte first / low word first  
 * 41AE 5256  ->  low byte first  / high word first 
 * 5256 41AE  ->  low byte first  / low word first   = "little endian"
 * */


/* * 
 * Supported Register Function codes:
 * +----------------+--------+--------------------------------------------+
 * | Function Code	| Action |         Table Name                         |
 * +----------------+--------+--------------------------------------------+
 * |  04 (04 hex)	  |  Read  |   Analog Input Registers                   |
 * |  03 (03 hex)	  |  Read  |   Analog Output Holding Registers          |
 * |  06 (06 hex)	  |  Write |   single	Analog Output Holding Register    |
 * |  16 (10 hex)	  |  Write |   multiple	Analog Output Holding Registers |
 * +----------------+--------+--------------------------------------------+
 * */

/* * 
 * Supported Coil Function codes:
 * +----------------+--------+----------------------------------+
 * | Function Code	| Action |        Table Name                |
 * +----------------+--------+----------------------------------+
 * | 02 (02 hex)	  |  Read  |   Discrete Input Contacts        |
 * | 01 (01 hex)	  |  Read  |   Discrete Output Coils          |
 * | 05 (05 hex)	  |  Write |   single	Discrete Output Coil    |
 * | 15 (0F hex)	  |  Write |   multiple	Discrete Output Coils |
 * +----------------+--------+----------------------------------+
 * */


// Estados de funcionamento do sistema 
#define HR_STATE_AUTO          0

#define HR_STATE_QUADRANT_1   01
#define HR_STATE_QUADRANT_2   02
#define HR_STATE_QUADRANT_3   03
#define HR_STATE_QUADRANT_4   04
#define HR_STATE_QUADRANT_12  12
#define HR_STATE_QUADRANT_23  23
#define HR_STATE_QUADRANT_34  34
#define HR_STATE_QUADRANT_41  41

#define HR_STATE_GO_HOME      253
#define HR_STATE_WAITING      254
#define HR_STATE_OFF          255
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

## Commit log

2024-08-12 Sistema funcionando / SDCard ruim ainda
    [SUP_INC.SLDPRT, SUP_INC.STL, SUP_MAG.SLDPRT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]
2024-08-20 update 20/8/2024
    [data.csv]
2024-09-14 Fix issues from v2.Rev
    [equ_out.csv, equ_pri.csv, sol_inv.csv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]
2024-11-18 Backup 18-11-2024
    [equ_out.csv, equ_pri.csv, sol_inv.csv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]
2024-11-22 fix: plot sensor Mag by I2C
    [AS5600.cpp, SensorI2C.h, main.cpp]
2024-11-23 Documento de TCC corrigido e terminado :D
2025-03-20 EOW: Finalizando trabalho, organizando repositorio
    [1_Anel_Interno_Engrenagens.STL, 2_Anel_Interno_Rosca.STL, 3_Reducao_Anel.STL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]
2025-03-25 EOW: Add documentos de conclusão
